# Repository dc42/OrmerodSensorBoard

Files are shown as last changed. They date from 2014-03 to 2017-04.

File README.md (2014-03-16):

OrmerodSensorBoard
==================

Here are the design files for my Z-height sensor board add-on to the RepRapPro Ormerod 3D printer. This board replaces the original IR sensor board used for Z-probing. It has the following advantages over the original:

1. It uses modulated infrared light, which makes it much less sensitive to ambient infrared such as is found in sunlight and in incandescent artificial light.
2. The sensor board is mounted on the hot end so that the sensor head is in-line with the nozzle in the x-direction. This makes it much less sensitive to variations in head sag.
3. The board includes the facility to mount the hot end connectors, eliminating the need for the original 6-pin connector. The new connectors are more reliable and more easily disassembled. In particular, the crimp receptacles can more easily be removed from the connector shell.
4. The board can accommodate three Cree LEDs to direct light on the work being printed. Alternatively, it can provide 12V power to an LED strip, or a constant-current supply to external LEDs.
5. The board includes provision for thermostatic control of the hot end fan. The fan is turned on when the hot end temperature exceeds approximately 42C, or when the board detects a hot end temperature measurement fault.
6. The board can also support an experimental ultrasonic sensor. This allows z-probing to be done anywhere on the bed. Due to variation in the speed of sound with temperature, the ultrasonic sensor is a little temperature-sensitive, but this can be compensated in the firmware.

Work is in progress to adapt the board for capacitive height sensing.

For assembly and usage instructions, please visit: http://miscsolutions.wordpress.com/assembling-and-using-the-eschertech-ormerod-hot-end-board/

I supply bare boards, kits of parts with all SMD components ready-mounted, and fully assembled boards. Contact me via the RepRap Ormerod forum at http://forums.reprap.org/list.php?340 by sending a personal message to dc42.

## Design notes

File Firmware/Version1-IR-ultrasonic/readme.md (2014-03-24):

This folder contains the following files:

<ul>
<li>OrmerodSensor.cppproj - Atmel Studio 6 project file</li>
<li>OrmerodSensor.cpp - source code</li>
<li>ecv.h - macros to make the Design-by-Contract annotations (for Escher C Verifier) in the source code invisible to the compiler</li>
</ul>

The ATTINY45A fuse settings required are: low 0xFF, high 0xDF, extended 0xFF.

The source code and the above fuse settings assume that the 12MHz ceramic resonator is fitted on the board. If the ultrasonic functionality is not required then it should be possible to omit the resonator and use the internal 8MHz clock, by changing F_CPU in the source code to 8000000uL and adjusting the fuse settings appropriately.

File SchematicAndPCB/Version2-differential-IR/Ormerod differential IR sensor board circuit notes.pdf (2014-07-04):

## Ormerod differential IR sensor board circuit description

Refer to the schematic. The board provides the following functions:
1. Illumination (U2 D1 D2 D3). U2 provides constant current drive to LEDs D1 D2 D3. The current can be increased above the default 20mA by fitting a resistor at position R23. Refer to the BCR402U datasheet for details. The +12V and 0V pads allow alternative lighting to be connected.
2. Heater on indication (B1 D7 R8). Bridge rectifier B1 allows correct operation irrespective of the polarity of the heater drive voltage. R8 limits the LED current to 20mA or less for heater voltages of up to 14V.
3. Fan control (U1 Q1 D4 R6 R7). Microcontroller U1 monitors the hot end thermistor voltage via R6. It turns the fan on via R7 and Q1 if either the temperature exceeds about 40C or the thermistor appears to be not connected. If R24 is not fitted then the firmware senses a high on pin PA4 and assumes that the Duet board uses a 1K thermistor series resistor. If R24 is fitted with a low value resistor (e.g. 1K) or a wire link, then the firmware senses a low on pin PA4 and assumes that a 4.7K series resistor is used. Series resistor R6 is included so that if either the 3.3V or the ground connection provided through connector X4 is broken, the effect on the temperature read by the Duet will be less severe and unlikely to result in serious overheating. Flyback diode D4 is included in case the fan presents an inductive load. A 0 ohm resistor or wire link can be added at position R22 if continuous operation of the fan is required.
4. Differential LED height sensor (D5 D6 D8 Q2 C1 C3 R1 R2 R3 R4 R5 R9). Microcontroller U1 measures the output from phototransistor Q2 with D6 and D5 both off, with D6 (the 'far' LED) on, and with D5 (the 'near' LED) on. Resistor R3 driving the near LED has a higher value than resistor R2 driving the far LED, to compensate for the shorter path taken by light reaching the phototransistor from the near LED. The firmware subtracts the reading with both LEDs off from each of the readings with one LED on in order to compensate for ambient IR, to provide a “far reading” and a “near reading”.

Pin PA0 on U1 determines the operating mode. The internal pullup resistor on pin PA0 is enabled, so that the pin is high if the 4th sensor wire from the Duet is not connected. When PA0 is high, the firmware operates in differential mode. When the far reading is substantially lower than the near reading, or the far reading is below a threshold, pins PA2 and PA7 are both driven low, so that the output on X4 pin 1 is 0V and the Duet sees a Z-probe reading close to zero. When the near reading is slightly below the far LED reading and the far LED reading is above threshold, PA2 is drive high and PA7 is driven low. This gives a z-probe reading of about 465. When the near reading is higher than the far reading and the far reading is above threshold, PA2 is driven low and PA7 high, resulting in a Z-probe reading of about 535. If either the near reading or the far reading is high enough to indicate that the phototransistor is saturated or approaching saturation, then both PA2 and PA7 are driven high, giving a Z probe reading close to 1023.

C3 serves not only to smooth out the supply voltage fluctuations due to the LEDs being turned on and off, but also to physically block the direct light path between the phototransistor and the photodiodes.

Resistor R9 and LED D8 provide an indication when the Z probe threshold has been reached.

If the control signal from the Duet on X4 pin 1 is driven low, then the sensor operates in simple modulated IR mode. In this mode, U1 pin PA7 is driven high if the near reading exceeds a fixed threshold. Pin PA2 remains low unless the phototransistor is saturated or approaching saturation, in which case both PA2 and PA7 are driven high to provide a Z probe reading of about 1023.
5. L1, C2 and C3 provide decoupling for U1. The ICSP pads allow U1 to be programmed.
6. Pads PAD1 through PAD7 and the pads for resistors R20 R21 are provided to facilitate modification and experimentation.

Version 1 by D Crocker, 2014-07-04.

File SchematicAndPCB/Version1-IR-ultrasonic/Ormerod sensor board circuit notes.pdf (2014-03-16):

## Ormerod sensor board circuit description

[Version 1, 2014-03-16]

Refer to the schematic. The board is designed to be populated in several different ways:
1. Modulated IR sensor, with modulation controlled by the Duet. The components fitted are:
U1 Q1 C1 C5 R2 R3 R4 R5 R13 L1 X5
The modulation signal from the Duet arrives via X5-1 and switches transistor Q2 via resistor R13. Q2 controls current flow through the IR emitter inside U1 via R5 to give a current of about 40mA when the modulation signal is high. R4 provides a base level of IR illumination even when the modulation signal is off, in order to bias the phototransistor in U1 into its linear region and reduce the effect of ambient IR. The phototransistor current causes a voltage drop across R2. C1 reduces capacitive pickup of noise from other wires in the loom. L1 and C5 decouple the incoming 3.3V supply. L1 is probably not needed n this configuration, so it could be replaced by a 0 ohm resistor. 1a. Modulated IR sensor + lighting. This is as option 1 plus the following components:
U3 D1 D2 D3 R14 X1 X2 X3 X6
In this configuration, all the hot end connectors are brought on to the board, replacing the function of the original 6-way connector. R14 completes the fan circuit. U3 provides a 20mA constant current source for LEDs D1 D2 D3. Optional resistor R1 can be added to increase the LED current, subject to keeping the current and power dissipation in U3 within its ratings.
2. Modulated IR sensor + fan control. The components populated are:
U1 U2 Q1 D4 C1 C2 C3 R2 R4 R5 R7 R10 R11 R12 L1 X1 X2 X3 X5 X6
In this mode, the modulation is controlled by the microcontroller U2, so the modulation control wire from the Duet is not needed. The microcontroller modulates the IR via R12 and Q2 (note that R13 is not fitted in this configuration). The signal appearing across R2 is fed to U2 pin 12 (ADC1) for synchronous detection. The mcu generates PWM signals at pins 6 and 8, which are combined by R7 and R10 and smoothed by C3 to provide an analog output. The mcu also controls the fan via R11 and Q1. D4 is a flyback diode for the fan, in case the fan presents an inductive load. The hot end thermistor is monitored via pin 10 of U2.
2a. Modulated IR sensor + fan + lighting. As option 2 plus U3 D1 D2 D3 and optionally R1.
3. Ultrasonic option. This is option 2 or 2a with the following additional components populated: XT1 L2 C4 R6 R8 R9
The microcontroller U2 produces a square wave at the appropriate frequency (41.67kHz) on pin 7. This is fed to the transducer connected at X4 via R6 and L2, with C4 completing the circuit while avoiding a DC bias across the transducer. R8 and R9 reduce the peak signal to remain in the range 0 to +3.3V and feed this signal to pin 11 (ADC2) of U2. U2 performs synchronous detection of the signal on this pin.
The mcu operates in IR mode when the signal at X5-1 is high or not connected, and in ultrasonic mode when the signal at X5-1 is low. A ceramic resonator is used instead of the built-in RC oscillator, in order to maintain an accurate frequency for the transducer.

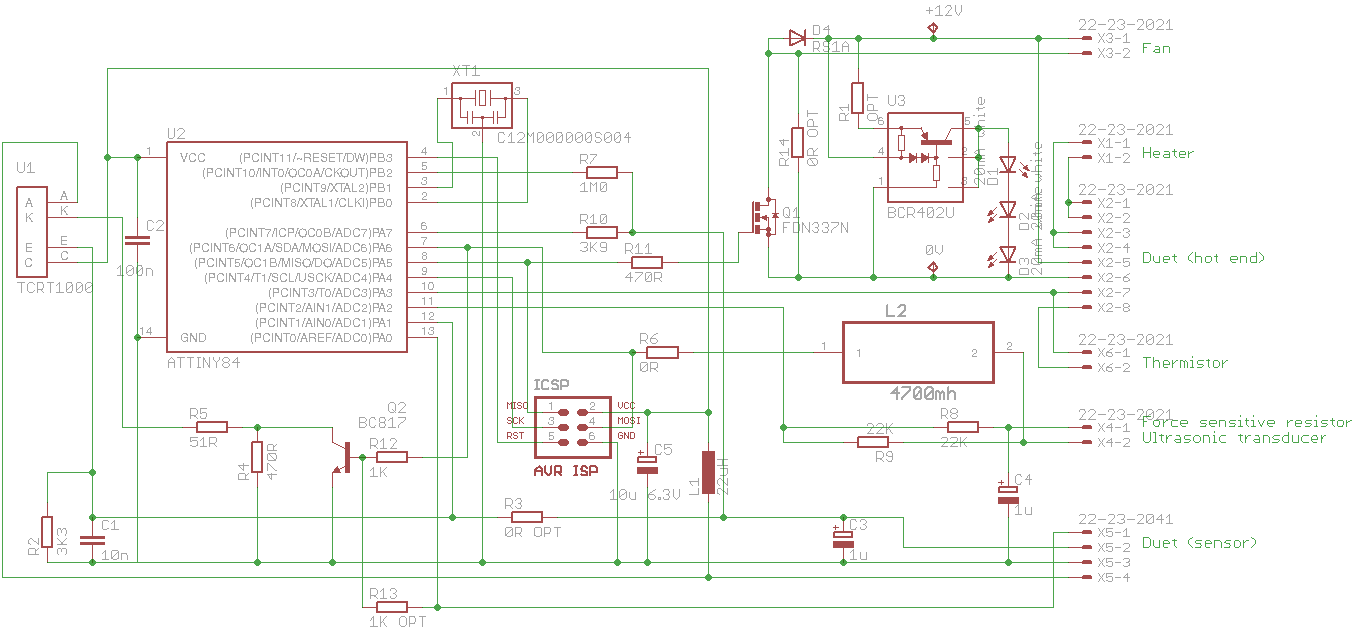
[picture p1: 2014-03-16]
SchematicAndPCB/Version1-IR-ultrasonic/schematic.png

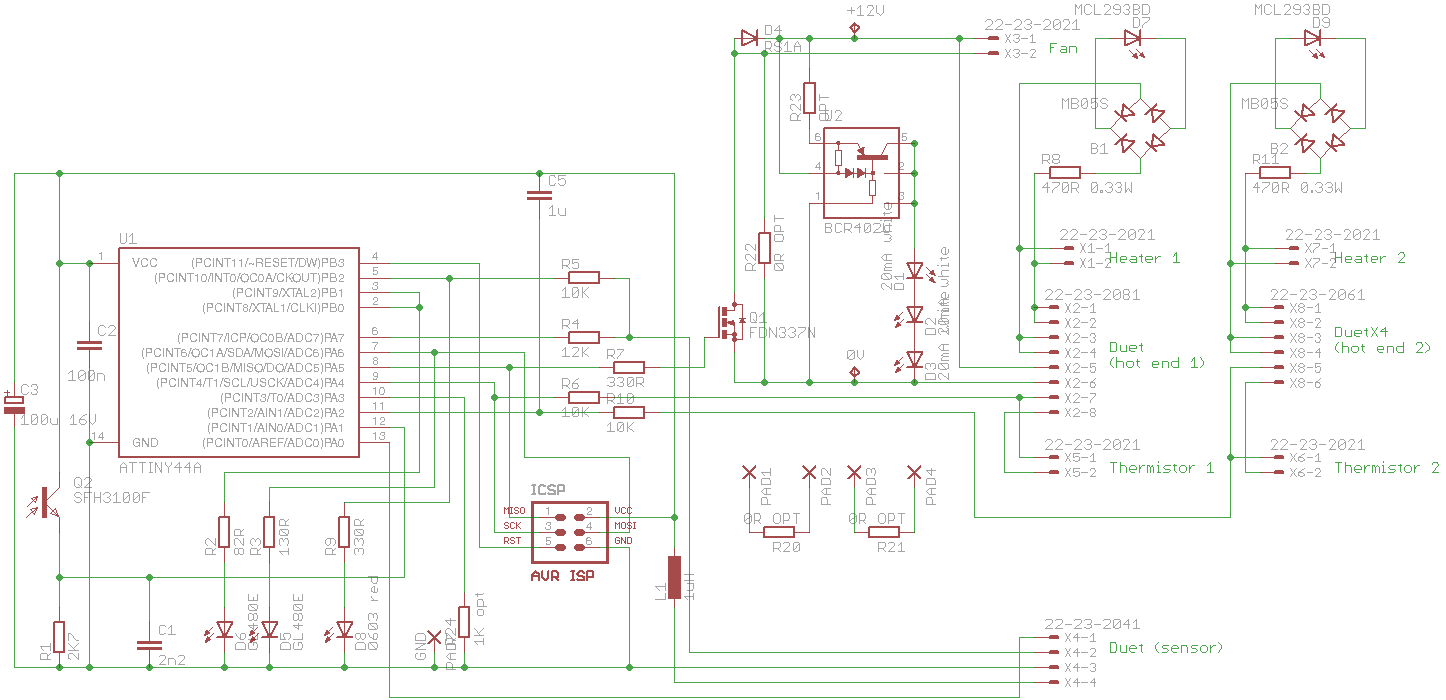
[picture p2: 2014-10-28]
SchematicAndPCB/Version2-differential-IR/schematic-dual-nozzle.png

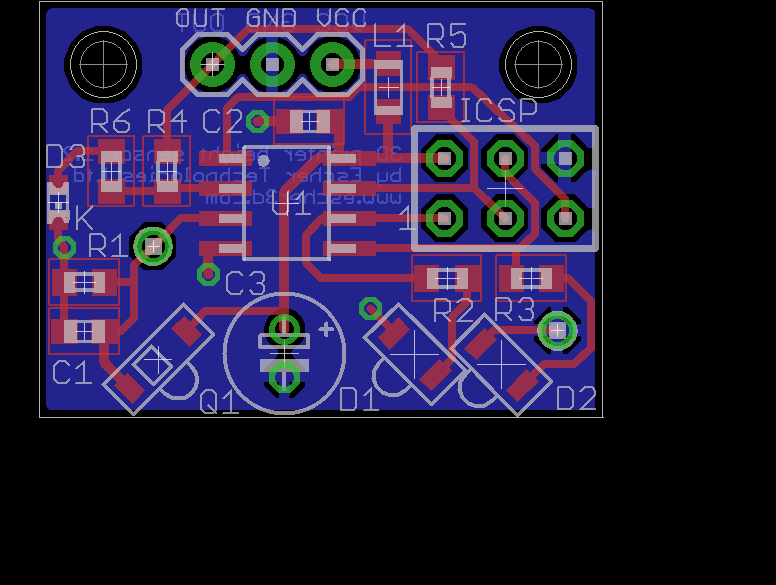
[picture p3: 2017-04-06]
SchematicAndPCB/Mini-differential-IR/V1.2/board.png

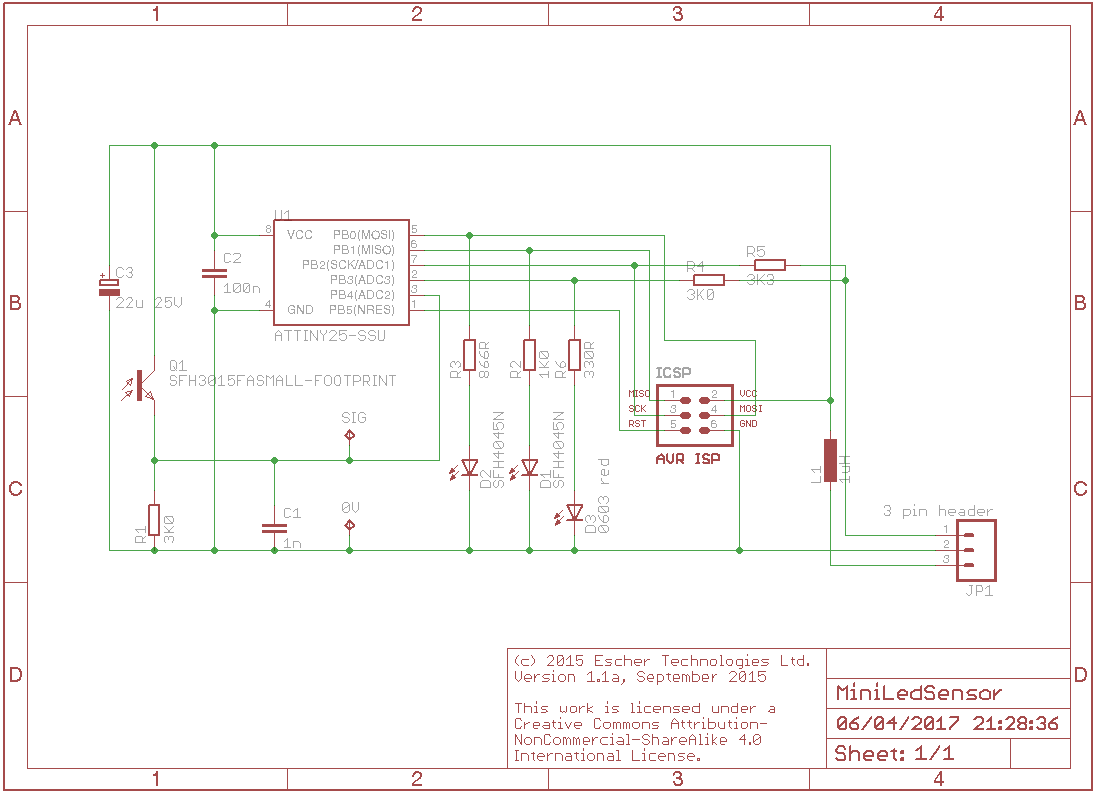
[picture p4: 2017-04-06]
SchematicAndPCB/Mini-differential-IR/V1.2/schematic.png

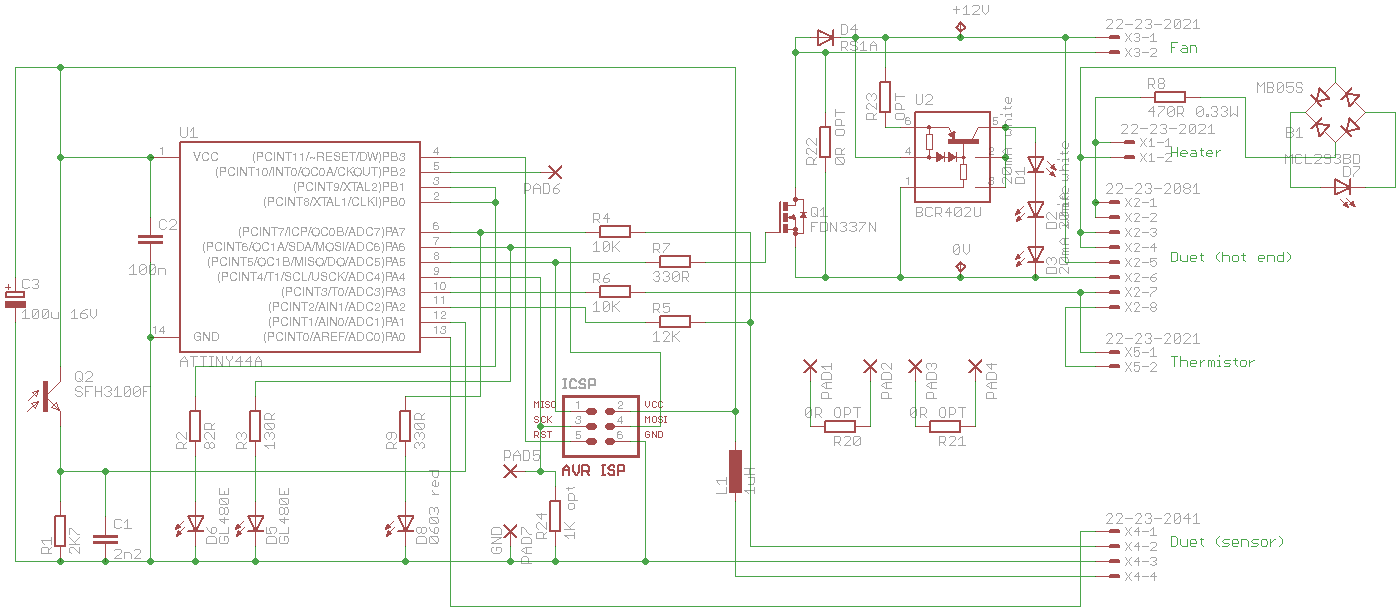
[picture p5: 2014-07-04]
SchematicAndPCB/Version2-differential-IR/schematic-single-nozzle.png

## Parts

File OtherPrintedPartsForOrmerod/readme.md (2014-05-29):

Other printed parts for Ormerod
===============================

This folder contains designs for the following printed parts, that are for the Ormerod but not for the sensor board:

1. PSU enclosure: this is an enclosure to cover the mains wiring and output wiring of a 12V 300W power supply sourced from eBay UK (http://www.ebay.co.uk/itm/UK-Stock-DC-12V-Universal-Regulated-Switching-Power-Supply-for-LED-Strip-CCTV-/161081134308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). This replaces the ATX PSU supplied with the kit and supplies a more stable and adjustable 12V supply, which is useful when printing ABS. It accommodates a snap-in IEC mains inlet with switch and fuse, a neon indicator, and a 20A locking connector for the 12V output. All of these can be sourced from Maplin Electronics or from the usual component distributors.

2. Spacers for Matt's y-belt fastening posts. Y-belt slippage is a common problem with Ormerods, and Matt's y-belt mounts at https://github.com/iamburny/OrmerodUpgrades/blob/master/y-belt-clamp-v7.stl solve the problem. However, getting the y-belt tension right can be tricky because the y-belt length can only be adjusted in multiples of a whole tooth. One solution is to print Matt's y-belt tensioning device too. A simpler solution is to print these spacers to slip under the y-belt posts before tightening the mounting screws. There are 3 different thicknesses of spacer in this print, which can be used individually or in combination to get the right y-belt tension.

3. Fan inlet duct and finger guard. This is a variation on the fan inlet duct by Andy (kwikius), designed for the 7-bladed fan shipped with some Ormerod kits, and thin enough to allow the print head to slide past the Duet electronics enclosure in its normal position. His original design is here http://forums.reprap.org/read.php?340,287558,291659#msg-291659. Hint: when fitting the Duet enclosure, push the three T-nuts into the extrusion, then rotate the one nearest the y-motor into position, then push the Duet enclosure as far towards the y-motor as it will go. By rotating the nut first, you gain a few extra mm clearance between the enclosure and the hot end fan.

4. Ormerod button push: a pair of button pushers to allow the Erase and Reset buttons to be activated through the holes in the Duet enclosure back cover.

5. X-carriage: a re-working of the X-carriage in OpenScad. This version does not have the mounting points for the IR sensor, because my own IR sensor board is mounted on the hot end instead. It has an optional slot for a force-sensitive resistor, however the area around the slot needs reinforcing if you enable this option.

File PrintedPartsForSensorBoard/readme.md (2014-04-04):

Printed parts to go with Ormerod sensor board
=============================================

To use the Ormerod sensor board you will need to print three parts:

1(a) Modified x-motor-bracket3.stl: Modified x-motor bracket. This includes an extended x-homing tab to suit the new position of the IR sensor head. Not needed if you use a microswitch for x-homing instead. Thanks to johneato for providing this.

1(b) sensorpad.stl: As an alternative to printing the modified x-motor bracket, you can print this add-on sensor pad and attach it to the original X motor bracket. Thanks to stevelup for providing this.

2(a) Modified heatsink-duct12.stl: Modified heatsink duct. This includes the mounting points for the sensor board.Thanks to johneato for providing this.

2(b) one-piece-hotend-airduct-with-new-irsensor-2.stl: Modified version of Matt's one-piece heatsink/fan duct. Thanks to Matt (iamburny) for modifying his design to add the supports and mounting holes for the sensor board. I have further modified his design by replacing the T-shaped cable tie point at the top centre by a cable tie loop at the top right, and making the cable management piece stronger. To use the one-piece duct you need to drill an additional hole in the heatsink so that you can rotate it 90 degrees.

3(a) Insulator.stl: This prevents the board from shorting against the z-threaded rod or other metal parts if the print head moves beyond the intended x-homing position. Alternatively, for kit 2 or 3 you can use Kim brown's safety cover, his files are at http://www.thingiverse.com/thing:272634.

3(b) Insulator-for-ultrasonic.stl: Thicker insulator which includes a holder for the ultrasonic transducer. This is thicker and longer than Insulator.stl to ensure that it touches the Z-nut trap before the ultrasonic sensor touches the threaded rod. If you use this part, you may have to extend the x-homing tab even further in the X-direction than the modified x-motor bracket already does, for example by sticking a piece of white card on top of it.

3(c) Insulator-thick.stl: Thick insulator, for use when the ultrasonic sensor is glued on the pcb behind and slightly to the left of the IR sensor.

Also in this folder:

BoardHolder.stl: This can be fixed to the back of a solder stencil, allowing boards to be accurately aligned with the stencil prior to application of solder paste.

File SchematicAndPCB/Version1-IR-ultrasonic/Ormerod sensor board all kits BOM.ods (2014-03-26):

Ormerod sensor board BOM |  | Last revision 2014-03-26
 |  |  |  | ------------- Qty required ------------
Item | Value or part # | Designators | Farnell # | Kit 2 | Kit 3 | Kit 4 | Kit 4+ | Kit 5 | Notes
Through hole parts
Connector | Molex 22-23-2021 | X1 X3 X4 X6 | 1462926 |  | 3 | 3 | 3 | 4 | X4 fitted on kit 5 only
Connector | Molex 22-23-2041 | X5 | 1462920 | 1 | 1 | 1 | 1 | 1
Connector | Molex 22-23-2081 | X2 | 1756826 |  | 1 | 1 | 1 | 1
Connector | 2x3 header | ICSP |  |  |  |  |  |  | Not fitted - only needed for programming
Sensor | TCRT1000 | U1 | 1470064 | 1 | 1 | 1 | 1 | 1
LED | Cree C535A-WJN-CU0V0231 | D1 D2 D3 | 1855547 |  | 3 | 3 | 3 | 3
Capacitor | 3.3nF 10% ceramic X7R | - | 1216424 |  |  |  |  | 0 or 1 | See note 1
Non-mounted parts
10mm 40kHz xmtr | Multicomp MCUST10P40B07RO |  | 2362667 |  |  |  |  | 1 | See note 1
Shell | Molex 22-01-2025 |  | 143126 |  | 3 | 3 | 3 | 4
Shell | Molex 22-01-2045 |  | 143128 | 1 | 1 | 1 | 1 | 1
Shell | Molex 22-01-2085 |  | 143130 |  | 1 | 1 | 1 | 1
Crimp pins | Molex 08-50-0032 |  | 9731474 | 4 | 18 | 18 | 18 | 20 | Plus a few spares
2way shell | Multicomp 2226A-02 |  | 1593506 | 1 | 1 |  |  | 1
Crimp pins | Multicomp 2226TG |  | 1593529 | 1 | 1 |  |  | 1
1m white wire 10/0.1 |  |  |  | 1 | 1 |  |  | 1
Screw | M2.5x10mm countersunk |  |  | 2 | 2 | 2 | 2 | 2
SMD parts
IC | ATTINY44A-SSU | U2 | 1699395 |  |  | 1 | 1 | 1
IC | BCR402U | U3 | 1791063 |  | 1 | 1 | 1 | 1
Transistor | BC817-40 | Q2 | 1798081 | 1 | 1 | 1 | 1 | 1
Mosfet | FDN337N | Q1 | 9845356 |  |  | 1 | 1 | 1
Diode | RS1A | D4 | 4085000 |  |  | 1 | 1 | 1 | Flyback diode for fan
12MHz resonator | AEL C12M000000S004 | XT1 | 1448144 |  |  |  | 1 | 1 | Alternative part AWSCR-12.00CV-T
Inductor | 1uH TDK MLZ2012A1R0WT | L1 | 2215638 | 1 | 1 | 1 | 1 | 1 | Must have low enough resistance
Inductor | 4.7mH EPCOS B82442H1475K | L2 | 3877474 |  |  |  | 1 | 1 | For driving ultrasonic transducer
Capacitor | 10u 6.3V tantalum case A | C5 | 1754143 | 1 | 1 | 1 | 1 | 1
Capacitor | 1u 1206 tantalum 10V+ 10% | C3 C4 | 1457411 |  |  | 1 | 2 | 2
Capacitor | 10n 0603 X7R | C1 | 1759022 | 1 | 1 | 1 | 1 | 1
Capacitor | 100n 0603 X7R | C2 | 1759016 |  |  | 1 | 1 | 1
Resistor | 0R 0603 | R3 |  | 1 | 1 |  |  |  | For direct sensor connection when U2 not fitted
Resistor | 0R 0603 | R6 |  |  |  |  | 1 | 1 | To reduce ultrasonic transducer drive if needed
Resistor | 0R 0603 | R14 |  |  | 1 |  |  |  | Bypasses fan control when Q1 not fitted
Resistor | 51R 0603 | R5 |  | 1 | 1 | 1 | 1 | 1
Resistor | 470R 0603 | R4 |  | 1 | 1 | 1 | 1 | 1
Resistor | 470R 0603 | R11 |  |  |  | 1 | 1 | 1
Resistor | 1K 0603 | R12 |  |  |  | 1 | 1 | 1
Resistor | 1K 0603 | R13 |  | 1 | 1
Resistor | 3K3 0603 | R2 |  | 1 | 1 | 1 | 1 | 1
Resistor | 3K9 0603 | R10 |  |  |  | 1 | 1 | 1
Resistor | 22K 0603 | R8 R9 |  |  |  |  | 2 | 2 | See note 1
Resistor | 1M0 0603 | R7 |  |  |  | 1 | 1 | 1
Resistor | As required 0603 | R1 |  |  |  |  |  |  | For increasing LED current
Notes
1 | Kit 5 early uses alternative ultrasonic transducer Murata MA40S4S (Farnell part number 1777667, also available from RS and from Conrad Electronics). This transducer produces less output, so the value of R8 is changed to 1M. A capacitor of about 3.3nF needs to be connected in parallel with this transducer to tune it. The Multicomp transducer does not require a tuning capacitor.

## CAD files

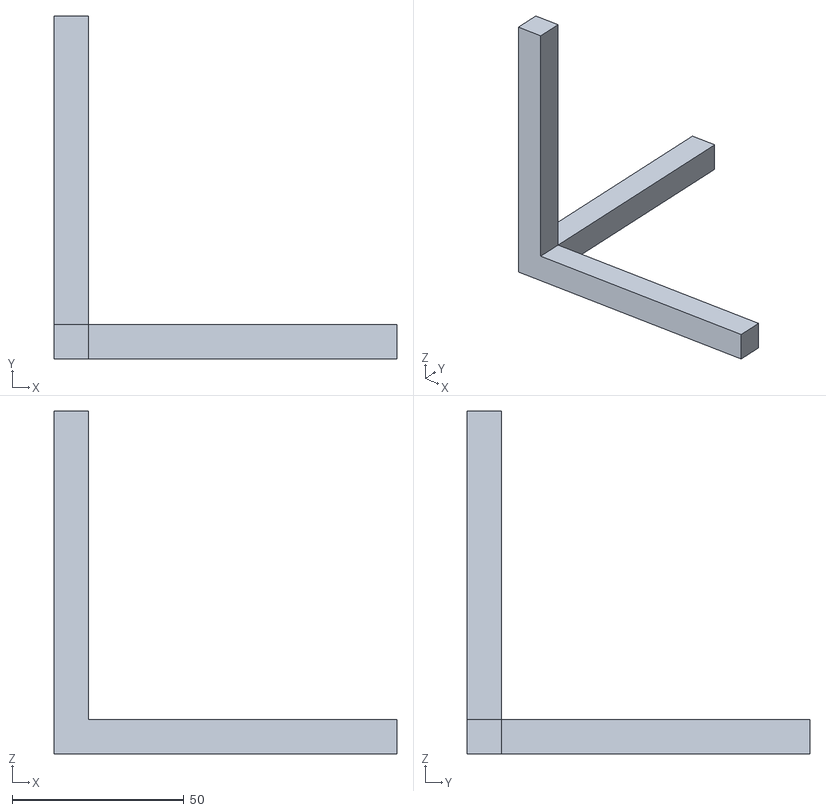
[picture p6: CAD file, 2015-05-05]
OtherPrintedPartsForOrmerod/OrthogonalCalibrationPiece.stl
100.0 x 100.0 x 100.0

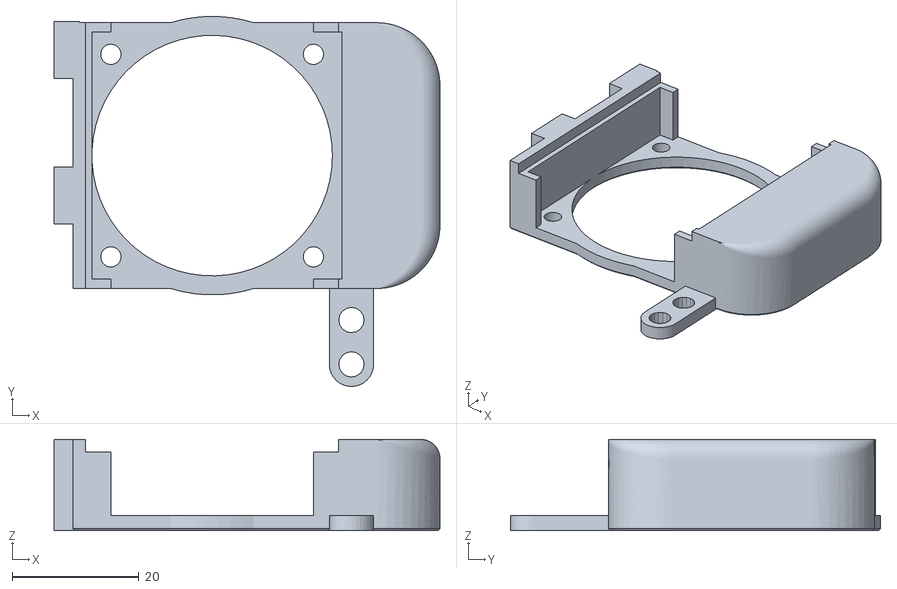
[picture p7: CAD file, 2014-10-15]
PrintedPartsForSensorBoard/modified-heatsink-duct-0.5mm-lower.stl
61.0 x 58.5 x 14.4

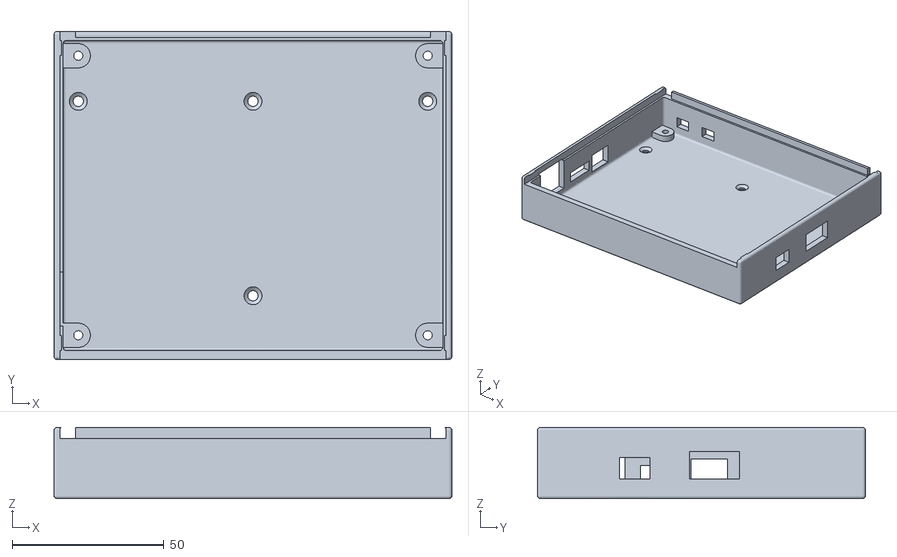
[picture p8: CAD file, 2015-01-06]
OtherPrintedPartsForOrmerod/DuetEnc-MiniKossel.stl
131.0 x 108.0 x 23.5

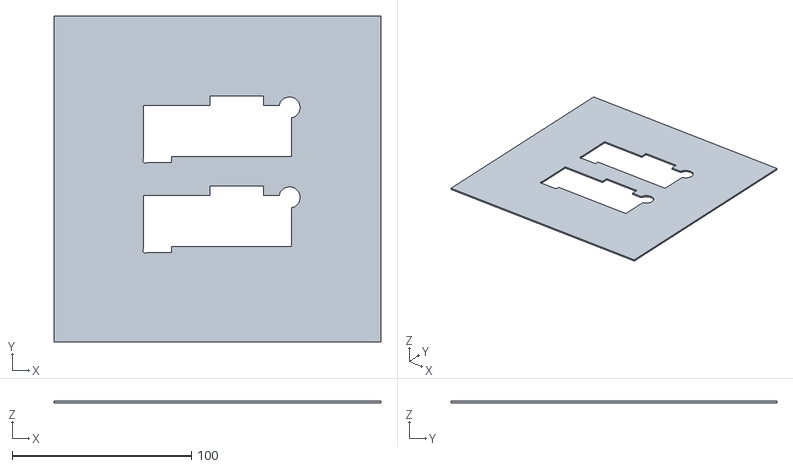
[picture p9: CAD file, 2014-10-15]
PrintedPartsForSensorBoard/BoardHolder-diff-led.stl
182.4 x 181.8 x 1.10

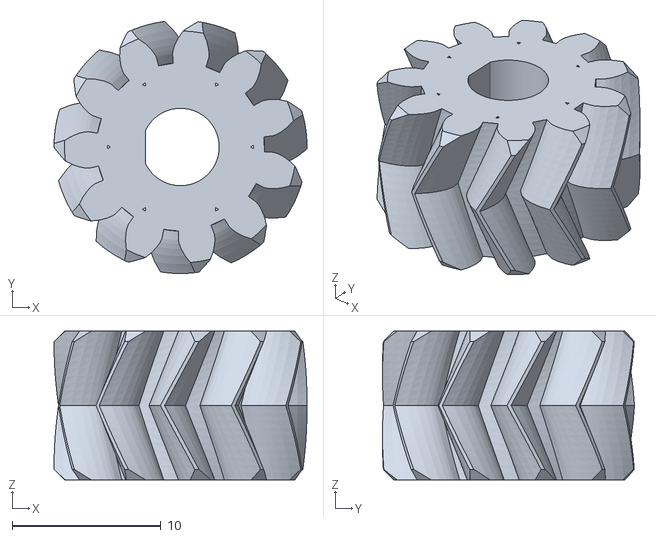
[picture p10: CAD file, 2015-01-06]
OtherPrintedPartsForOrmerod/iamburnyExtruderSmallGearModified.stl
17.0 x 17.0 x 10.0

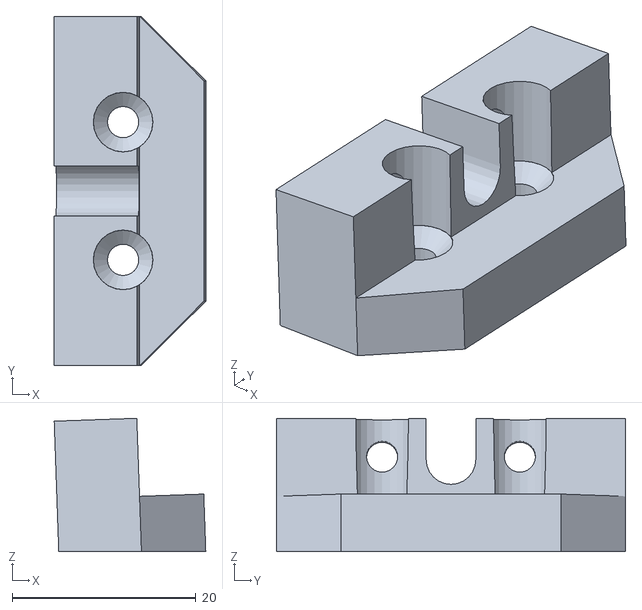
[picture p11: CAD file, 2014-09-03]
OtherPrintedPartsForOrmerod/NozzleMountStandard-2deg.stl
16.5 x 38.0 x 14.5

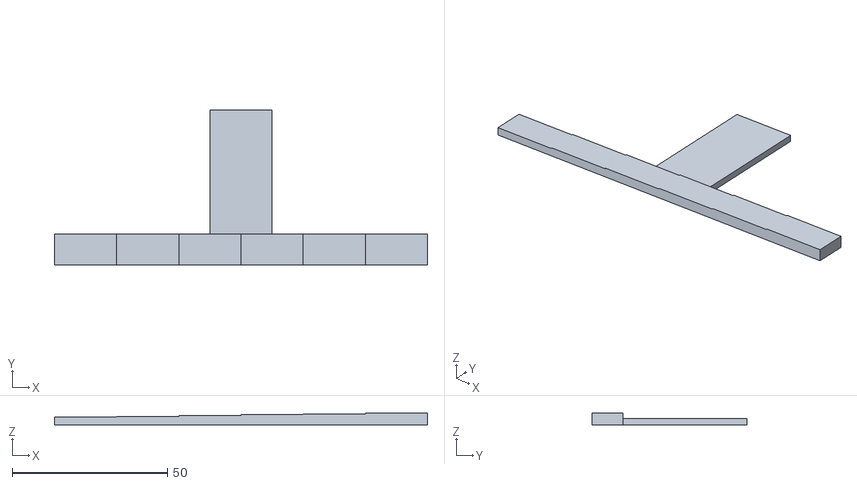
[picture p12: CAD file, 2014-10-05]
PrintedPartsForSensorBoard/LedBoardTestJig.stl
120.0 x 50.0 x 3.75

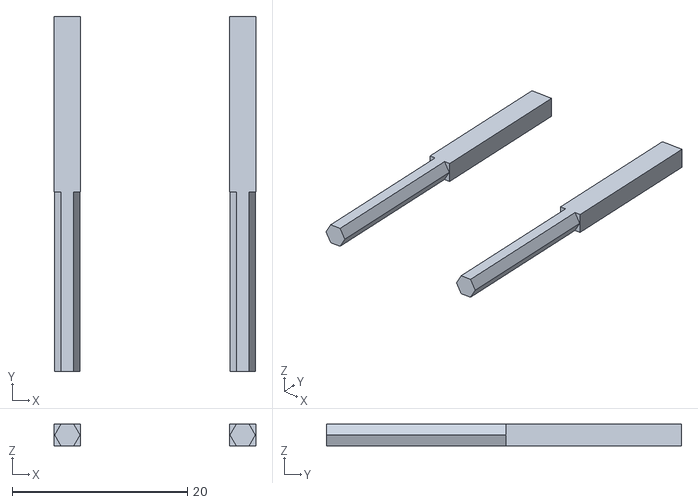
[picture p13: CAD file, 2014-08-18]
OtherPrintedPartsForOrmerod/OrmerodButtonPush.stl
23.0 x 40.5 x 2.50

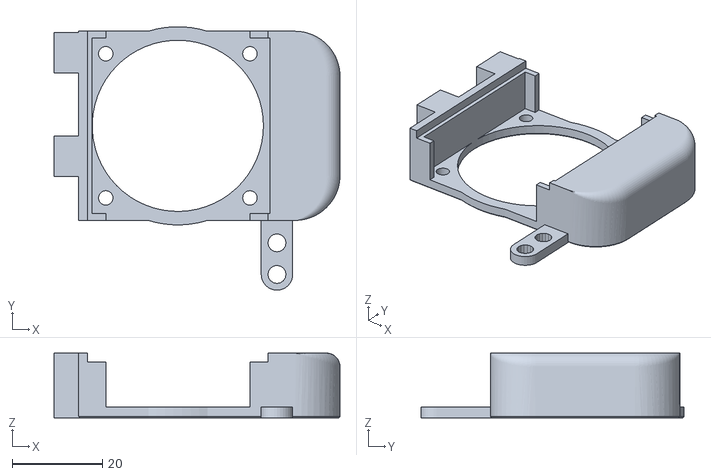
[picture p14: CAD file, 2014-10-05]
PrintedPartsForSensorBoard/modified-heatsink-duct-dual-nozzle.stl
63.5 x 58.5 x 14.4

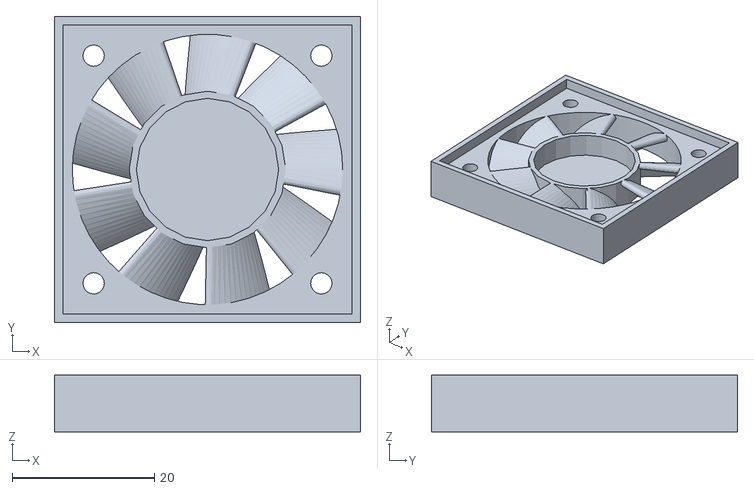
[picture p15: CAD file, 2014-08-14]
OtherPrintedPartsForOrmerod/FanDeflector.stl
43.0 x 43.0 x 8.00

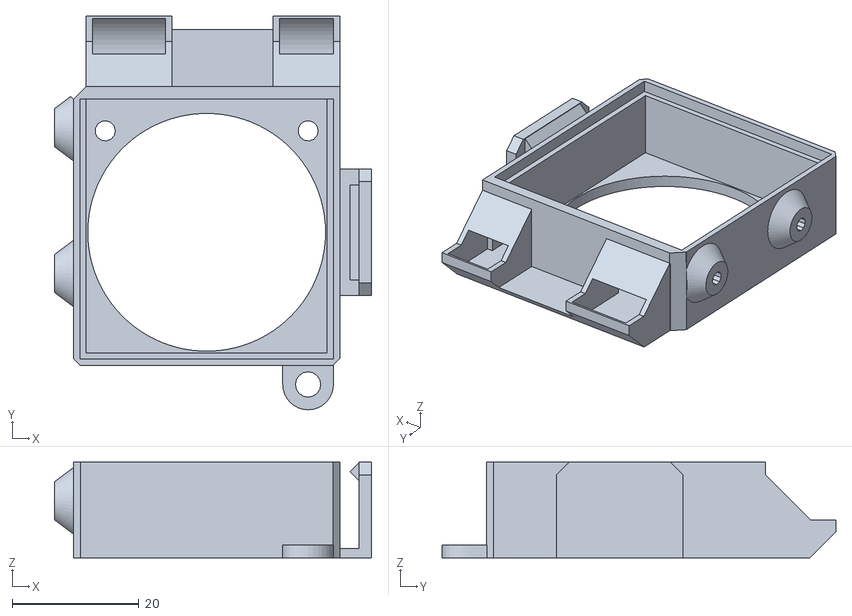
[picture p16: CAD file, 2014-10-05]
PrintedPartsForSensorBoard/one-piece-hotend-airduct-with-new-irsensor-1mm-lower.stl
50.0 x 62.1 x 15.1

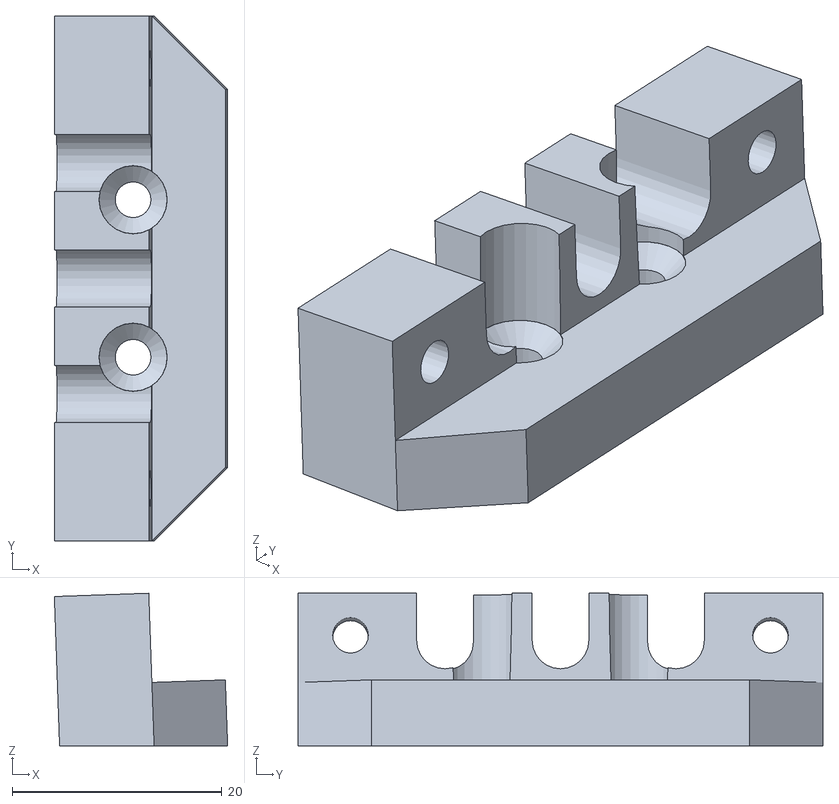
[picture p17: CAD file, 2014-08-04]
OtherPrintedPartsForOrmerod/NozzleMount-1or2-2deg.stl
16.5 x 50.0 x 14.5

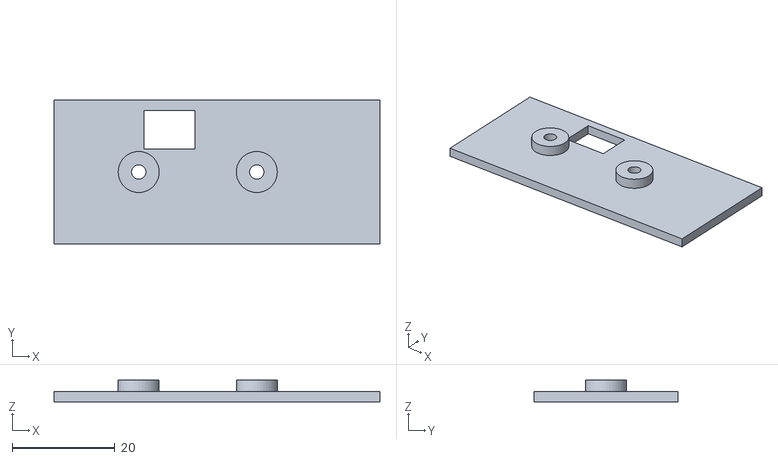
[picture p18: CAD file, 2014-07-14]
PrintedPartsForSensorBoard/Insulator-diff-led-dual-nozzle.stl
63.5 x 28.0 x 4.25

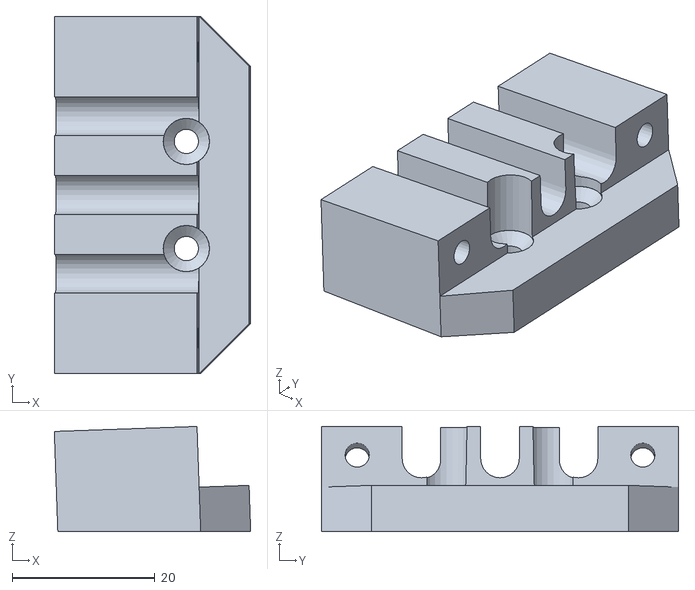
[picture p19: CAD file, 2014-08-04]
OtherPrintedPartsForOrmerod/NozzleMount-1or2-2deg-long.stl
27.5 x 50.0 x 14.7

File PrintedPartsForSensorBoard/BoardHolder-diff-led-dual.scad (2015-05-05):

// Holder for Ormerod prototype differential IR sensor board
// Choose layer height to be a submultiple of the thickness

thickness=1.1;	// board is 1.2mm but this part comes out slightly too thick
xborder=30;
yborder=30;
yrepeat=70;
height=82.07375;
width=29.00;
nibWidth=3.0;
nibHeight=15.5;	//actually 14.605
upperWidth=43.35;
upperHeight=38;
clearance=0.35;
cornerRadius=1.5;
cornerOffset=1;
overlap=1;

module wedge(x,y,z)
{
	polyhedron(
		points=[[0,0,0],[x,0,0],[0,y,0],[0,0,z],[x,0,z],[0,y,z]],
		faces=[[0,2,1],[3,4,5],[0,1,3],[1,4,3],[1,2,4],[2,5,4],[0,3,2],[5,2,3]]
	);
}

module boardCutout()
{
	translate([0,nibWidth,-overlap])
		cube([height+clearance,width+clearance,thickness+2*overlap]);
	translate([height-upperHeight,nibWidth,-overlap])
		cube([upperHeight+clearance,upperWidth+clearance,thickness+2*overlap]);
	translate([0,0,-overlap])
		cube([nibHeight,nibWidth+overlap,thickness+2*overlap]);
	translate([height+clearance-cornerOffset,upperWidth+nibWidth+clearance-cornerOffset,-overlap])
		cylinder(r=6,h=thickness+2*overlap,$fn=12);
}


difference()
{
	cube([height+2*xborder+clearance,upperWidth+nibWidth+2*yborder+clearance+yrepeat,thickness]);
	translate([xborder,yborder,0]) boardCutout();
	translate([xborder,yborder+yrepeat,0]) boardCutout();
}

translate([12-overlap,16-overlap,0]) wedge(10+2*overlap,10+2*overlap,thickness);

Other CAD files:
PrintedPartsForSensorBoard/modified-heatsink-duct-single-nozzle.stl
PrintedPartsForSensorBoard/original-rrp-fan-duct.stl
OtherPrintedPartsForOrmerod/DuetEncX4.stl
PrintedPartsForSensorBoard/modified-fan-duct.stl
PrintedPartsForSensorBoard/BoardHolder-diff-led-mini.scad
PrintedPartsForSensorBoard/BoardHolder-diff-led.scad
PrintedPartsForSensorBoard/BoardHolder.scad
OtherPrintedPartsForOrmerod/DuetEnc-MiniKossel.scad
OtherPrintedPartsForOrmerod/DuetEnc.scad
OtherPrintedPartsForOrmerod/DuetEnc.stl
OtherPrintedPartsForOrmerod/DuetEncMeasure.scad
OtherPrintedPartsForOrmerod/FanDeflector.scad
OtherPrintedPartsForOrmerod/NozzleMount.scad
OtherPrintedPartsForOrmerod/NozzleMount.stl
OtherPrintedPartsForOrmerod/OrmerodButtonPush.scad
OtherPrintedPartsForOrmerod/OrthogonalCalibrationPiece.scad
OtherPrintedPartsForOrmerod/PSU.scad
OtherPrintedPartsForOrmerod/PSU.stl
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

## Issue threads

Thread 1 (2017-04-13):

Schematic note

timmit99, 2017-04-13:
Just looking through for replacement part numbers and it seems that on the V1.2 differential sensor board schematic you did not change the Version number in the  V1.2 schematic. It still says V1.1a, September 2015.

There is no indication other than the file's path that it is ACTUALLY the V1.2 schematic.

timmit99, 2017-04-13:
https://raw.githubusercontent.com/dc42/OrmerodSensorBoard/master/SchematicAndPCB/Mini-differential-IR/V1.0_1.1/schematic.png

https://raw.githubusercontent.com/dc42/OrmerodSensorBoard/master/SchematicAndPCB/Mini-differential-IR/V1.2/schematic.png

dc42, 2017-04-13:
You are right, I forgot to update the version number in the text on the schematic. But it's definitely the version 1.2 schematic, it has the right part numbers for the phototransistor and IR LEDs.

timmit99, 2017-04-13:
thanks, Just bashed into the sensor and bent one of the IR LED's back and when i tried to reorient it the legs snapped. I got 2 of them on the way from Mouser.

dc42, 2017-04-13:
If the IR LEDs have legs then you have the version 1.0 or 1.1 board. The part numbers on the 1.2 schematic are SMD parts that won't fit your board.

timmit99, 2017-04-13:
Yep, that's why i was checking the two versions because we have one V1.1 and one V1.2 board. That's when i noticed that the version numbering was off and just wanted to post here to avoid any further confusion. The broken board is a V1.1 so i have the sfh4141 coming. Thanks for the awesome board!

Closed 2017-04-13.

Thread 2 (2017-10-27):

v1.3 hardware is out but schematics are missing here.

lf-, 2017-10-27:
[Spool3D](https://spool3d.ca/mini-differential-ir-height-sensing-board/) says that they have "v1.3" boards, but I only see v1.2 here if the commit history is to be believed.

Also, the link to the schematic PNG in [this blog post](https://miscsolutions.wordpress.com/mini-height-sensor-board/) is broken.

dc42, 2017-10-28:
The schematic for version 1.3 is the same as for version 1.2. Only the PCB layout is different.

amrithmmh, 2018-04-24:
can you share the schematics? the link seems broken

amrithmmh, 2018-04-24:
thanks for making the circuit
Is this possible to use it with glass (stuck with 3M blue tape on top) ?

lf-, 2018-04-24:
Consider reading the blog post detailing the project [here](
https://miscsolutions.wordpress.com/mini-height-sensor-board/) which states
supported surface types.

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

Deneteus, 2019-01-27:
Why were changes needed for the PCB layout between 1.2 and 1.3 if the schematic was the same?

dc42, 2019-01-28:
To make manufacturing easier.

Deneteus, 2019-01-31:
Is there any reason it cannot be made smaller? Say doing the same design but with edge mounted SMD sensors?

dc42, 2019-01-31:
The width could be slightly smaller, it is limited by the spacing needed between the phototransistor and the outer IR diode. The height could be reduced by using a attiny44a MCU in a flat pack package instead of attiny25 and smaller connectors and programming pads, or perhaps a single 6-way connector for both. We intended to switch to a JST 1.5mm connector but we had push back from one of our OEM customers.

Closed 2019-04-06.

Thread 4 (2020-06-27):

Hardcode to digital output mode

3dlpm, 2020-06-27:
Hi,

I am using the Escher 3D mini IR sensor board (V1.2) with a RUMBA board, which has a three pin Z- endstop connectors. It provides 5V on VCC, GND and has a signal input, which can be internally pulled up. Using the rumba with Marlin would easily work, but I am using the RUMBA with Klipper firmware, which runs on a separate host CPU (Raspberry Pi) and controls the RUMBA, which has a small version of firmware that executes the motion commands that the Klipper host sends it.

I am having issues with the mini sensor board starting in analog output mode (4 LED flashes) because Klipper sometimes takes a while to start (or restart, if you changed config) so the firmware in the RUMBA does not set the internal pull-ups on the Z- signal pin on time for the mini-sensor board to detect.
I basically have to cycle the power or disconnect the mini board connectors every time, sometimes repeatedly, until the internal pull-ups are set by klipper. It is very annoying and inconsistent to get the mini-sensor board started in digital output mode.

I would like to simply hard code the mini sensor board so that it always starts in digital output mode. I am not a programmer and I don't have enough knowledge to modify/verify and upload the mini sensor board's firmware. Do you have a workaround or suggestion for how to hard code the sensor board to always start in digital mode?

I think this is something that should be implemented as a jumper (solder) on the board.

Thank you

dc42, 2020-06-27:
Hi,

Why not add an external pullup resistor between OUT and VCC? That would
be easier than reprogramming it.

Regards

David Crocker, Escher Technologies Ltd.
http://www.eschertech.com
Tel. +44 (0)20 8144 3265 or +44 (0)7977 211486

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

3dlpm, 2020-06-27:
Yes, I could try that. What value do you recommend?

dc42, 2020-06-27:
I suggest between 20K and 100K.

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

--
Sent from my Android device with K-9 Mail. Please excuse my brevity.

3dlpm, 2020-06-29:
Thanks David.
It is working fine with a 39Kohm external pull-up

Closed 2020-06-29.

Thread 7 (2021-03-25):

Calibration of DIY version of your sensor

deHarro, 2021-03-25:
Hi David, @dc42

I built a clone IR-sensor from the schematics you provided.
It sort of works, but I think I have to do some calibration before I get decent results.
Is there any calibration instruction available, you can provide me with, please?

Thanks!
Harry

deHarro, 2021-04-18:
I realized that the calibration data are never read back from EEPROM, so perhaps this calibration thing is not use at all.

Harry

Closed 2021-04-18.

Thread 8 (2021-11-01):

TMC2209/UART + ir sensor has inconsistent readings.

mpalpha, 2021-11-01:
What component do I need and where do I add it? to block the interference?

mpalpha, 2021-11-02:
Trying a 25v 47uf capacitor between. Gnd/5v pins. Hope it works.

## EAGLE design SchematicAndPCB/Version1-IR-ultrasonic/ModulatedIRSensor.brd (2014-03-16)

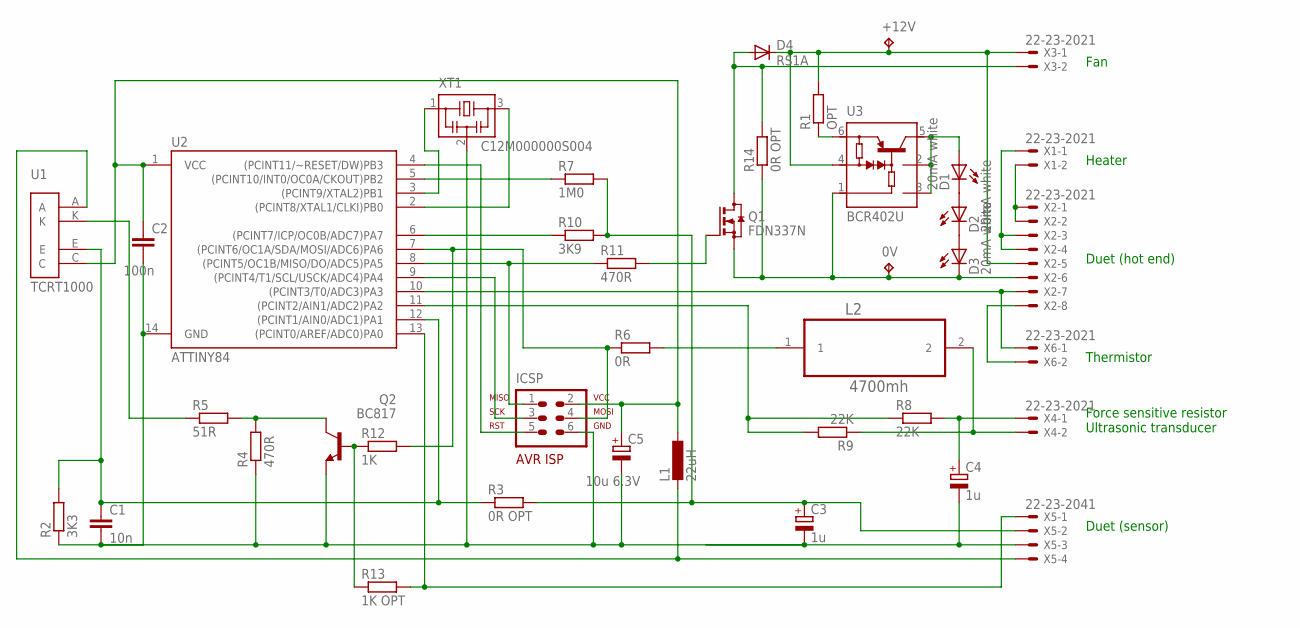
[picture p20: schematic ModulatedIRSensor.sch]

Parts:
0V: TPPAD1-13; P1-13
+12V: TPPAD1-13; P1-13
C1: 10n; C0603
C2: 100n; C0603
C3, C4: 1u; SMC_A
C5: 10u 6.3V; SMC_A
D1, D2, D3: 20mA white; LED5MM
D4: RS1A; DO214AC
ICSP: AVR-ISP-6VERT; AVR-ISP-6
L1: 22uH; L2012C
L2: 4700mh; INDC5650X530N
Q1: FDN337N; SOT23
Q2: BC817; SOT23
R1: OPT; R0603
R2: 3K3; R0603
R3, R14: 0R OPT; R0603
R4, R11: 470R; R0603
R5: 51R; R0603
R6: 0R; R0603
R7: 1M0; R0603
R8, R9: 22K; R0603
R10: 3K9; R0603
R12: 1K; R0603
R13: 1K OPT; R0603
U1: TCRT1000
U2: ATTINY84; SO14
U3: BCR402U; SC74_INFINEON
X1, X3, X4, X6: 22-23-2021
X2: 22-23-2021; 22-23-2081
X5: 22-23-2041
XT1: C12M000000S004; CSTCR6M

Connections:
GND: C1.2, C2.2, C3.-, C4.-, C5.-, ICSP.6, Q2.2 (E), R2.1, R4.1, U2.14 (GND), X5.3, XT1.2
GND2: 0V.TP, D3.K (C), Q1.2 (S), R14.1, U3.1 (GND), X2.6
LED: D1.A, U3.2 (IOUT2), U3.3 (IOUT3), U3.5 (IOUT1)
unnamed: L1.2, U1.A, X5.4
unnamed: L2.2, R9.1, X4.2
unnamed: ICSP.5, U2.4 ((PCINT11/~RESET/DW)PB3)
unnamed: ICSP.1, R11.1, U2.8 ((PCINT5/OC1B/MISO/DO/ADC5)PA5)
unnamed: ICSP.3, U2.9 ((PCINT4/T1/SCL/USCK/ADC4)PA4)
unnamed: ICSP.4, R6.1, R12.2, U2.7 ((PCINT6/OC1A/SDA/MOSI/ADC6)PA6)
unnamed: R1.1, U3.6 (REXT)
unnamed: D1.K (C), D2.A
unnamed: U2.10 ((PCINT3/T0/ADC3)PA3), X2.7, X6.1
unnamed: X1.2, X2.1, X2.2
unnamed: D2.K (C), D3.A
unnamed: C3.+, R3.2, R7.2, R10.2, X5.2
unnamed: D4.A, Q1.3 (D), R14.2, X3.2
unnamed: X1.1, X2.3, X2.4
unnamed: X2.8, X6.2
unnamed: R5.1, U1.K
unnamed: L2.1, R6.2
unnamed: Q2.3 (C), R4.2, R5.2
unnamed: R7.1, U2.5 ((PCINT10/INT0/OC0A/CKOUT)PB2)
unnamed: C4.+, R8.2, X4.1
unnamed: R10.1, U2.6 ((PCINT7/ICP/OC0B/ADC7)PA7)
unnamed: R8.1, R9.2, U2.11 ((PCINT2/AIN1/ADC2)PA2)
unnamed: Q1.1 (G), R11.2
unnamed: Q2.1 (B), R12.1, R13.1
unnamed: C1.1, R2.2, R3.1, U1.E, U2.12 ((PCINT1/AIN0/ADC1)PA1)
unnamed: R13.2, U2.13 ((PCINT0/AREF/ADC0)PA0), X5.1
unnamed: U2.2 ((PCINT8/XTAL1/CLKI)PB0), XT1.3
unnamed: U2.3 ((PCINT9/XTAL2)PB1), XT1.1
VCC: C2.1, C5.+, ICSP.2, L1.1, U1.C, U2.1 (VCC)
VS+12V: +12V.TP, D4.C, R1.2, U3.4 (VIN), X2.5, X3.1

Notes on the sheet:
Heater
Duet (hot end)
Thermistor
Duet (sensor)
Force sensitive resistor Ultrasonic transducer
Fan
TCRT1000

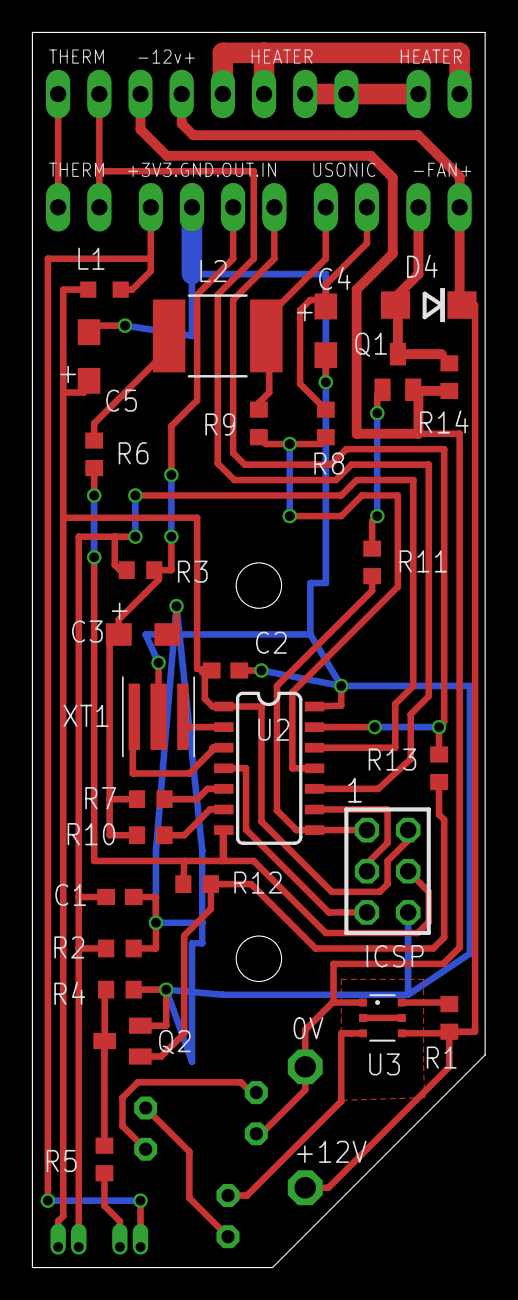
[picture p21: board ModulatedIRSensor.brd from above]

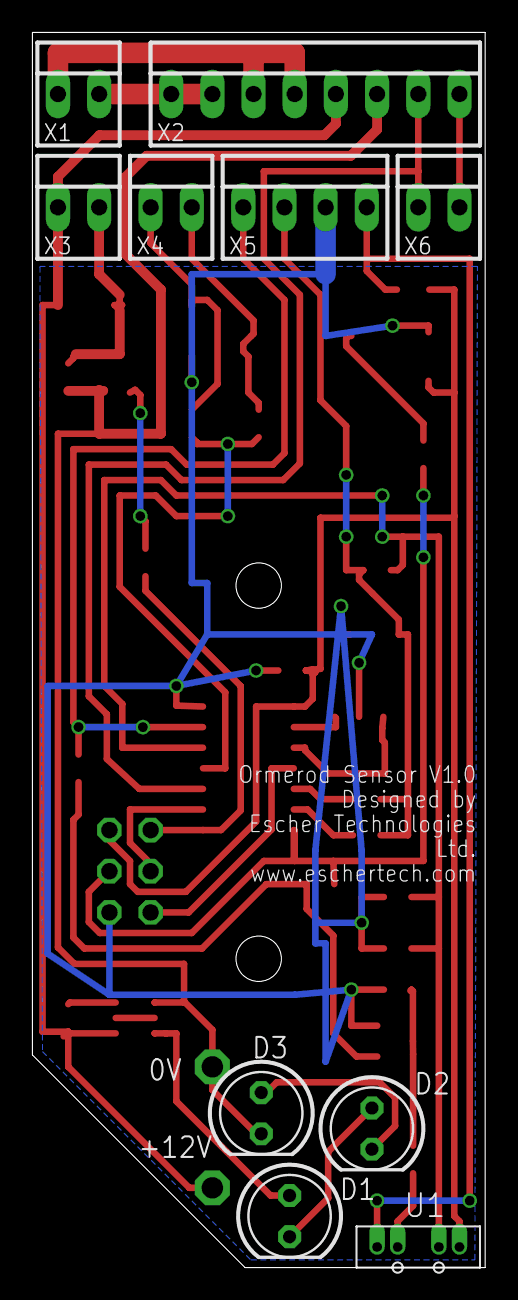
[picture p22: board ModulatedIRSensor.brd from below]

Board: 2 copper layers, 27.9 x 76.2 mm, 40 parts (12 on the bottom side), 33 nets.

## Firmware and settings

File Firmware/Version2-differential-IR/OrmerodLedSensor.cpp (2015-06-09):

/*
 * OrmerodLedSensor.cpp
 *
 * Created: 16/02/2014 21:15:50
 *  Author: David
 */ 

#include <ecv.h>

#ifdef __ECV__
#define __attribute__(_x)
#define __volatile__
#define __DOXYGEN__				// this avoids getting the wrong definitions for uint32_t etc.
#endif

#ifdef __ECV__
#pragma ECV noverifyincludefiles
#endif

#include <avr/io.h>
#include <avr/interrupt.h>
#include <avr/eeprom.h>
#include <avr/wdt.h>

#ifdef __ECV__
#pragma ECV verifyincludefiles
#endif

#define DUAL_NOZZLE (1)		// set nonzero for dual nozzle support
#define ISR_DEBUG	(0)		// set nonzero to use PB2 as debug output pin

#if DUAL_NOZZLE && ISR_DEBUG
#error "DUAL_NOZZLE and ISR_DEBUG may not both be set"
#endif

#define BITVAL(_x) static_cast<uint8_t>(1u << (_x))

// Pin assignments:
// PA0/ADC0		digital input from Duet
// PA1/ADC1		analog input from phototransistor
// PA2/ADC2		output to Duet via 12K resistor (single nozzle) OR analog input from thermistor2 (dual nozzle)
// PA3/ADC3		analog input from thermistor (single nozzle) or 1K/4K7 sense pin (dual nozzle)
// PA4/SCLK		1K/4K7 sense pin (single nozzle) or analog input from thermistor 1 (dual nozzle). Also SCLK when programming.
// PA5/OC1B		digital output to control fan, active high. Also MISO when programming.
// PA6/OC1A		near LED drive, active low in prototype, will be active high in release. Also MOSI when programming.
// PA7/OC0B		output to Duet via 10K resistor

// PB0			far LED drive, active high
// PB1			far LED drive, active high (paralleled with PB0)
// PB2/OC0A		unused (single nozzle) OR ISR-DEBUG pin OR output to Duet via 12K resistor (dual nozzle)
// PB3/RESET	not available, used for programming

__fuse_t __fuse __attribute__((section (".fuse"))) = {0xE2u, 0xDFu, 0xFFu};

const unsigned int PortADuetInputBit = 0;
const unsigned int AdcPhototransistorChan = 1;
#if DUAL_NOZZLE
const unsigned int AdcThermistor2Chan = 2;
const unsigned int PortASeriesResistorSenseBit = 3;
const unsigned int AdcThermistor1Chan = 4;
#else
const unsigned int PortADuet12KOutputBit = 2;
const unsigned int AdcThermistor1Chan = 3;
const unsigned int PortASeriesResistorSenseBit = 4;
#endif
const unsigned int PortAFanControlBit = 5;
const unsigned int PortANearLedBit = 6;
#if DUAL_NOZZLE
const unsigned int PortADuet12KOutputBit = 7;
#else
const unsigned int PortADuet10KOutputBit = 7;
#endif

const uint8_t PortAUnusedBitMask = 0;

const uint8_t PortBFarLedMask = BITVAL(0) | BITVAL(1);
#if DUAL_NOZZLE
const unsigned int PortBDuet10KOutputBit = 2;
const uint8_t PortBUnusedBitMask = 0;
#elif ISR_DEBUG
const unsigned int PortBDebugPin = 2;
const uint8_t PortBUnusedBitMask = 0;
#else
const uint8_t PortBUnusedBitMask = BITVAL(2);
#endif

// Approximate MPU frequency (8MHz internal oscillator)
const uint32_t F_CPU = 8000000uL;

// IR parameters. These also allow us to receive a signal through the command input.
const uint16_t interruptFreq = 8000;						// interrupt frequency. We run the IR sensor at one quarter of this, i.e. 2kHz
															// highest usable value is about 9.25kHz because the ADC needs 13.5 clock cycles per conversion.
const uint16_t divisorIR = (uint16_t)(F_CPU/interruptFreq);
const uint16_t baseTopIR = divisorIR - 1;
const uint16_t cyclesAveragedIR = 8;						// must be a power of 2, max 32 (unless we make onSumIR and offSumIR uint32_t)

const uint16_t farThreshold = 10 * cyclesAveragedIR;		// minimum far reading for us to think the sensor is working properly
const uint16_t simpleNearThreshold = 30 * cyclesAveragedIR;	// minimum reading to set output high in simple mode
const uint16_t saturatedThreshold = 870 * cyclesAveragedIR;	// minimum reading for which we consider the sensor saturated

// IR variables
typedef uint8_t invariant(value < cyclesAveragedIR) irIndex_t;

struct IrData
{
	uint16_t readings[cyclesAveragedIR];
	volatile uint16_t sum;
	irIndex_t index;

	void addReading(uint16_t arg)
	writes(*this; volatile)
	pre(invar())
	pre(arg <= 1023)
	post(invar())
	{
		sum = sum - readings[index] + arg;
		readings[index] = arg;
		index = static_cast<irIndex_t>((index + 1) % cyclesAveragedIR);
	}
	
	void init()
	writes(*this; volatile)
	post(invar());

	ghost(
		bool invar() const
			returns((forall r in readings :- r <= 1023) && sum == + over readings);
	)
	
#ifdef __ECV__
	// Dummy constructor to keep eCv happy
	IrData() : index(0) {}
#endif
};

IrData nearData, farData, offData;
	
// Fan parameters
const uint16_t thermistorSampleFreq = 16;
const uint16_t thermistorSampleIntervalTicks = interruptFreq/thermistorSampleFreq;

#if DUAL_NOZZLE
const uint16_t thermistorSamplesAveraged = 8;			// reduced from 16 because it looks like we ran out of memory in the dual nozzle case
#else
const uint16_t thermistorSamplesAveraged = 16;
#endif

// Fan thresholds

// Using a 1K series resistor, we use the ADC in differential mode with a gain of 1 and full scale resolution of 512, but we reverse the inputs so we effectively get 2x extra gain.
const uint16_t thermistorConnectedThreshold1K = 30;		// we consider the hot end thermistor to be disconnected if we get this reading less than the reference, or a higher reading
const uint16_t thermistorOffThreshold1K = 340;			// we turn the fan off if we get this reading less than the reference (about 38C), or a higher reading
const uint16_t thermistorOnThreshold1K = 400;			// we turn the fan on if we get this reading less than the reference (about 42C), or lower reading

// Using a 4K7 series resistor, we use the ADC in single-ended mode with a gain of 1.
const uint16_t thermistorConnectedThreshold4K7 = 7;		// we consider the hot end thermistor to be disconnected if we get this reading less than the reference, or a higher reading
const uint16_t thermistorOffThreshold4K7 = 78;			// we turn the fan off if we get this reading less than the reference (about 38C), or a higher reading
const uint16_t thermistorOnThreshold4K7 = 92;			// we turn the fan on if we get this reading less than the reference (about 42C), or lower reading

const uint16_t fanOnSeconds = 2;						// once the fan is on, we keep it on for at least this time

// Thermistor and fan variables
typedef uint8_t invariant(value < thermistorSamplesAveraged) thermistorIndex_t;

struct ThermistorData
{	
	uint16_t readings[thermistorSamplesAveraged], offsets[thermistorSamplesAveraged];
	volatile uint16_t readingSum, offsetSum;
	thermistorIndex_t index;

	void init(uint16_t readingInit, uint16_t offsetInit)
	writes(*this; volatile)
	pre(readingInit <= 1023; offsetInit <= 1023)
	post(this->invar());

	ghost(
		bool invar() const
		returns(   (forall r in readings :- r <= 1023)
				&& (forall r in offsets :- r <= 1023)
				&& readingSum == + over readings
				&& offsetSum == + over offsets
			   );
	)

#ifdef __ECV__
	// Dummy constructor to keep eCv happy
	IrData() : index(0) {}
#endif
};

ThermistorData thermistor1Data;
#if DUAL_NOZZLE
ThermistorData thermistor2Data;
#endif

uint16_t thermistorConnectedThreshold, thermistorOnThreshold, thermistorOffThreshold;
bool thermistor1Kmode;
uint16_t lastFanSampleTicks;
uint8_t fanChangeCount;

// General variables
volatile uint16_t tickCounter;						// counts system ticks, lower 2 bits also used for ADC/LED state
bool running;

/* ISR for the timer 0 compare match A interrupt
This works on a cycle of 16 readings as follows:

State	Just did	Doing now	New LED state	New ADC state
0		Dummy off	Far			Off				(Phototransistor)
1		Far			Off			Near			(Phototransistor)
2		Off			Near		Off				(Phototransistor)
3		Near		Dummy off	Far				(Phototransistor)
4		Dummy off	Far			Off				(Phototransistor)
5		Far			Off			Near			(Phototransistor)
6		Off			Near		Off				(Phototransistor)
7		Near		Dummy off	Far				(Phototransistor)
8		Dummy off	Far			Off				(Phototransistor)
9		Far			Off			Near			(Phototransistor)
10		Off			Near		Off				Thermistor
11		Near		Dummy fan	(Off)			(Thermistor)
12		Dummy fan	Dummy fan	(Off)			(Thermistor)
13		Dummy fan	Dummy fan	(Off)			(Thermistor)
14		Dummy fan	Fan			(Off)			Phototransistor
15		Fan			Dummy off	Far				(Phototransistor)

This pattern takes account of the following:
1. When we switch the ADC into differential mode to get reliable readings with a 1K series resistor, the ADC subsystem needs extra time to settle down.
2. We want to measure the readings with near and far LEDs illuminated from the off-state in both cases, so that the slow phototransistor response affects
   both readings equally.
*/

ISR(TIM1_COMPB_vect)
writes(nearData; farData; offData)
writes(thermistor1Data)
#if DUAL_NOZZLE
writes(thermistor2Data)
#endif
writes(volatile)
pre(nearData.invar(); farData.invar(); offData.invar())
pre(thermistor1Data.invar())
#if DUAL_NOZZLE
pre(thermistor2Data.invar())
#endif
post(nearData.invar(); farData.invar(); offData.invar())
post(thermistor1Data.invar())
#if DUAL_NOZZLE
post(thermistor2Data.invar())
#endif
{
#if ISR_DEBUG
	PORTB |= BITVAL(PortBDebugPin);					// set debug pin high
#endif

	uint16_t adcVal = ADC & 1023u;					// get the ADC reading from the previous conversion
	uint8_t locTickCounter = (uint8_t)tickCounter;
	while (TCNT1 < 3 * 64) {}						// delay a little until the ADC s/h has taken effect. 3 ADC clocks should be enough, and 1 ADC clock is 64 of our clocks.
	switch(locTickCounter & 0x0fu)
	{
		case 0:
		case 4:
		case 8:
			// Far LED is on, we just did a dummy off reading, we are doing a far reading now and an off reading next
			PORTB &= ~PortBFarLedMask;				// turn far LED off
			break;

		case 1:
		case 5:
		case 9:
			// LEDs are off, we just did a far reading, we are doing an off reading now and a near reading next			
			if (running)
			{
				farData.addReading(adcVal);
			}
			PORTA |= BITVAL(PortANearLedBit);		// turn near LED on
			break;

		case 2:
		case 6:
			// Near LED is on, we just did a, off reading, we are doing a near reading now and a dummy off reading next
			if (running)
			{
				offData.addReading(adcVal);
			}
			PORTA &= ~BITVAL(PortANearLedBit);		// turn near LED off
			break;

		case 3:
		case 7:
			// LEDs are off, we just did a near reading, we are doing a dummy off reading now and a far reading next
			if (running)
			{
				nearData.addReading(adcVal);
			}
			PORTB |= PortBFarLedMask;				// turn far LED on
			break;
			
		case 10:
			// Near LED is on, we just did an off reading, we are doing a near reading now and a fan reading next
			if (running)
			{
				offData.addReading(adcVal);
			}
			PORTA &= ~BITVAL(PortANearLedBit);		// turn near LED off

#if DUAL_NOZZLE
			if ((locTickCounter & 0x20u) == 0)
			{
				// Select thermistor 1
				if (thermistor1Kmode)
				{
					ADMUX = ((locTickCounter & 0x10u) != 0)
						? 0b00110011u				// +ve input = ADC4, -ve input = ADC3, gain x20
						: 0b00010011u;				// +ve input = ADC3, -ve input = ADC4, gain x20
				}
				else
				{
					ADMUX = (uint8_t)AdcThermistor1Chan;	// select thermistor 1 (ADC4) as a single-ended input
				}
			}
			else
			{
				// Select thermistor 2
				if (thermistor1Kmode)
				{
					ADMUX = ((locTickCounter & 0x10u) != 0)
						? 0b00010001u				// +ve input = ADC2, -ve input = ADC3, gain x20
						: 0b00110001u;				// +ve input = ADC3, -ve input = ADC2, gain x20
				}
				else
				{
					ADMUX = (uint8_t)AdcThermistor2Chan;	// select thermistor 2 (ADC2) as a single-ended input
				}
			}
#else
			if (thermistor1Kmode)
			{
				ADMUX = ((locTickCounter & 0x10u) != 0)
						? 0b00010011u				// +ve input = ADC3, -ve input = ADC4, gain x20
						: 0b00110011u;				// +ve input = ADC4, -ve input = ADC3, gain x20
			}
			else
			{
				ADMUX = (uint8_t)AdcThermistor1Chan;	// select thermistor 1 (ADC3) as a single-ended input
			}
#endif			
			break;
		
		case 11:
			// LEDs are off, we just did a near reading, we are doing a fan reading which we will discard, we will do another fan reading next
			if (running)
			{
				nearData.addReading(adcVal);
			}
			break;
			
		case 12:
		case 13:
			// LEDs are off and we are doing dummy fan readings
			break;

		case 14:
			// LEDs are off, we just did a dummy fan reading, we are doing another fan reading now and a dummy off reading next
			ADMUX = (uint8_t)AdcPhototransistorChan;	// select input 1 = phototransistor
			break;

		case 15:
			// LEDs are off, we just did a fan reading, we are doing an off reading now and a far reading next
			if (running)
			{
				ThermistorData* currentThermistor =
#if DUAL_NOZZLE
					((locTickCounter & 0x20u) == 0) ? &thermistor1Data : &thermistor2Data;
#else
					&thermistor1Data;
#endif
				if (thermistor1Kmode)
				{
					adcVal ^= 0x0200u;				// convert signed reading to unsigned biased by 512
					if ((locTickCounter & 0x10u) != 0)
					{
						currentThermistor->readingSum = currentThermistor->readingSum - currentThermistor->readings[currentThermistor->index] + adcVal;
						currentThermistor->readings[currentThermistor->index] = adcVal;
						currentThermistor->index = (currentThermistor->index + 1) & (thermistorSamplesAveraged - 1);
					}
					else
					{
						currentThermistor->offsetSum = currentThermistor->offsetSum - currentThermistor->offsets[currentThermistor->index] + adcVal;
						currentThermistor->offsets[currentThermistor->index] = adcVal;
					}
				}
				else
				{
					currentThermistor->readingSum = currentThermistor->readingSum - currentThermistor->readings[currentThermistor->index] + adcVal;
					currentThermistor->readings[currentThermistor->index] = adcVal;
					currentThermistor->index = (currentThermistor->index + 1) & (thermistorSamplesAveraged - 1);
				}
			}
			PORTB |= PortBFarLedMask;				// turn far LED on
			break;
	}
	
	++tickCounter;

#if ISR_DEBUG
	PORTB &= (uint8_t)(~BITVAL(PortBDebugPin) & 0xFFu);	// set debug pin high
#endif
}

// Delay for a little while
// Each iteration of the loop takes 4 clocks plus one clock per NOP instruction in the body.
// The additional overhead for the function, including calling it, is 12 clocks.
// Therefore, with F_CPU = 8MHz and using 4 NOP instructions, it delays n + 1.5 microseconds.
void shortDelay(uint8_t n)
{
	for (uint8_t i = 0; i < n; ++i)
	keep(i <= n)
	decrease(n - i)
	{
#ifndef __ECV__			// eCv doesn't understand asm
		asm volatile ("nop");
		asm volatile ("nop");
		asm volatile ("nop");
		asm volatile ("nop");
#endif
	}
}

// Check the fan
void checkFan()	
writes(fanChangeCount; volatile)
{
	if ((PORTA & BITVAL(PortAFanControlBit)) != 0)
	{
		// Fan is on. Turn it off if thermistor is connected and temp <= off-threshold
		if (   (thermistor1Data.readingSum < thermistor1Data.offsetSum)
#if DUAL_NOZZLE
			&& (thermistor2Data.readingSum < thermistor2Data.offsetSum)
#endif
		   )
		{
			uint16_t fanDiff1 = thermistor1Data.offsetSum - thermistor1Data.readingSum;
#if DUAL_NOZZLE
			uint16_t fanDiff2 = thermistor2Data.offsetSum - thermistor2Data.readingSum;
#endif
			if (   (fanDiff1 >= thermistorConnectedThreshold) && (fanDiff1 <= thermistorOffThreshold)
#if DUAL_NOZZLE
				&& (fanDiff2 >= thermistorConnectedThreshold) && (fanDiff2 <= thermistorOffThreshold)
#endif
			   )
			{
				if (fanChangeCount == 0)
				{
					PORTA &= (uint8_t)~BITVAL(PortAFanControlBit);	// turn fan off						
				}
				else
				{
					--fanChangeCount;
				}
			}
		}			
	}
	else
	{
		uint16_t fanDiff1;
#if DUAL_NOZZLE
		uint16_t fanDiff2;
#endif
		// Fan is off. Turn it on if thermistor is disconnected or temp >= on-threshold
		if (   (thermistor1Data.readingSum >= thermistor1Data.offsetSum)
			|| ((fanDiff1 = thermistor1Data.offsetSum - thermistor1Data.readingSum) < thermistorConnectedThreshold)
			|| (fanDiff1 >= thermistorOnThreshold)
#if DUAL_NOZZLE
			|| (thermistor2Data.readingSum >= thermistor2Data.offsetSum)
			|| ((fanDiff2 = thermistor2Data.offsetSum - thermistor2Data.readingSum) < thermistorConnectedThreshold)
			|| (fanDiff2 >= thermistorOnThreshold)
#endif
		   )
		{
			// We used to turn the fan on immediately, but now we delay it a little to try to improve noise immunity
			if (fanChangeCount >= fanOnSeconds * thermistorSampleFreq)
			{
				PORTA |= BITVAL(PortAFanControlBit);		// turn fan on			
			}
			else
			{
				fanChangeCount += 4;						// the time we wait before turning the fan on is 1/4 of the time we wait before turning it off
			}
		}		
	}
	
#ifndef __ECV__
	wdt_reset();											// kick the watchdog
#endif
}

// Give a G31 reading of about 0
inline void SetOutputOff()
writes(volatile)
{
	// We do this in 2 operations, each of which is atomic, so that we don't mess up what the ISR is doing with the LEDs.
#if DUAL_NOZZLE
	PORTB &= ~BITVAL(PortBDuet10KOutputBit);
	PORTA &= ~BITVAL(PortADuet12KOutputBit);
#else
	PORTA &= ~BITVAL(PortADuet10KOutputBit);
	PORTA &= ~BITVAL(PortADuet12KOutputBit);
#endif
}

// Give a G31 reading of about 465 indicating we are approaching the trigger point
inline void SetOutputApproaching()
writes(volatile)
{
	// We do this in 2 operations, each of which is atomic, so that we don't mess up what the ISR is doing with the LEDs.
#if DUAL_NOZZLE
	PORTB &= ~BITVAL(PortBDuet10KOutputBit);
	PORTA |= BITVAL(PortADuet12KOutputBit);
#else
	PORTA &= ~BITVAL(PortADuet10KOutputBit);
	PORTA |= BITVAL(PortADuet12KOutputBit);
#endif
}	

// Give a G31 reading of about 535 indicating we are at/past the trigger point
inline void SetOutputOn()
writes(volatile)
{
	// We do this in 2 operations, each of which is atomic, so that we don't mess up what the ISR is doing with the LEDs.
#if DUAL_NOZZLE
	PORTB |= BITVAL(PortBDuet10KOutputBit);
	PORTA &= ~BITVAL(PortADuet12KOutputBit);
#else
	PORTA |= BITVAL(PortADuet10KOutputBit);
	PORTA &= ~BITVAL(PortADuet12KOutputBit);
#endif
}
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
int main(void)
writes(volatile)
writes(running)
writes(nearData; farData; offData)	// IR variables
writes(thermistor1Data)
#if DUAL_NOZZLE
writes(thermistor2Data)
#endif
writes(fanChangeCount; lastFanSampleTicks)				// fan variables
writes(thermistor1Kmode; thermistorConnectedThreshold; thermistorOffThreshold; thermistorOnThreshold)
{
	cli();
#if DUAL_NOZZLE
	DIDR0 = BITVAL(AdcPhototransistorChan) | BITVAL(AdcThermistor1Chan) | BITVAL(AdcThermistor2Chan);
	// disable digital input buffers on ADC pins
#else
	DIDR0 = BITVAL(AdcPhototransistorChan) | BITVAL(AdcThermistor1Chan);
															// disable digital input buffers on ADC pins
#endif
	// Set ports and pullup resistors
	PORTA = BITVAL(PortADuetInputBit) | BITVAL(PortASeriesResistorSenseBit) | PortAUnusedBitMask;
															// enable pullup on Duet input, series resistor sense input, and unused I/O pins
	PORTB = PortBUnusedBitMask;								// enable pullup on unused I/O pins
	
	// Enable outputs
#if DUAL_NOZZLE
	DDRA = BITVAL(PortAFanControlBit) | BITVAL(PortANearLedBit) | BITVAL(PortADuet12KOutputBit);
#else
	DDRA = BITVAL(PortAFanControlBit) | BITVAL(PortANearLedBit) | BITVAL(PortADuet10KOutputBit) | BITVAL(PortADuet12KOutputBit);
#endif

#if DUAL_NOZZLE
	DDRB = PortBFarLedMask | BITVAL(PortBDuet10KOutputBit);	// enable LED and 12K outputs on port B
#elif ISR_DEBUG
	DDRB = PortBFarLedMask | BITVAL(PortBDebugPin);			// enable LED and debug outputs on port B
#else
	DDRB = PortBFarLedMask;									// enable LED outputs on port B
#endif
	
	// Wait 10ms to ensure that the power has stabilized before we read the series resistor sense pin
	for (uint8_t i = 0; i < 40; ++i)
	{
		shortDelay(255u);
	}
	thermistor1Kmode = ((PINA & BITVAL(PortASeriesResistorSenseBit)) != 0);
	
	// Initialize the fan so that it won't come on at power up
	uint16_t readingInit, offsetInit;
	if (thermistor1Kmode)
	{
		// When reading the thermistor in 1K series resistor mode, we run ADC in differential bipolar mode, gain = 20 (effective gain is 10 because full-scale is 512 not 1024)
		// We use the 1K mode sense pin as a +3.3V reference. Set it HIGH to reduce noise on it. We have already set the bit in the output register.
		DDRA |= BITVAL(PortASeriesResistorSenseBit);
		
		thermistorConnectedThreshold = thermistorConnectedThreshold1K * thermistorSamplesAveraged;
		thermistorOffThreshold = thermistorOffThreshold1K * thermistorSamplesAveraged;
		thermistorOnThreshold = thermistorOnThreshold1K * thermistorSamplesAveraged;
		offsetInit = 512;
		readingInit = offsetInit - thermistorConnectedThreshold1K;
	}
	else
	{
		// When reading the thermistor in 4.7K series resistor mode, we run ADC in single-ended mode, gain = 1
		thermistorConnectedThreshold = thermistorConnectedThreshold4K7 * thermistorSamplesAveraged;
		thermistorOffThreshold = thermistorOffThreshold4K7 * thermistorSamplesAveraged;
		thermistorOnThreshold = thermistorOnThreshold4K7 * thermistorSamplesAveraged;
		offsetInit = 1023;
		readingInit = offsetInit - thermistorConnectedThreshold4K7;
	}

	thermistor1Data.init(readingInit, offsetInit);
#if DUAL_NOZZLE
	thermistor2Data.init(readingInit, offsetInit);
#endif

	sei();

#ifndef __ECV__												// eCv++ doesn't understand gcc assembler syntax
	wdt_enable(WDTO_500MS);									// enable the watchdog (we kick it when checking the fan)	
#endif
		
	runIRsensorAndFan();									// doesn't return
	return 0;												// to keep gcc happy
}

// Initialize the IR data structure
void IrData::init()
{
	for (uint8_t i = 0; i < cyclesAveragedIR; ++i)
	writes(i; *this; volatile)
	keep(i <= cyclesAveragedIR)
	keep(forall j in 0..(i-1) :- readings[j] == 0)
	decrease(cyclesAveragedIR - i)
	{
		readings[i] = 0;
	}
	index = 0;
	sum = 0;
}

// Initialize the thermistor data structure
void ThermistorData::init(uint16_t readingInit, uint16_t offsetInit)
{
	readingSum = 0;
	offsetSum = 0;

	for (uint8_t i = 0; i < thermistorSamplesAveraged; ++i)
	writes(i; *this; volatile)
	keep(i <= thermistorSamplesAveraged)
	keep(forall j in 0..(i - 1) :- readings[j] == readingInit)
	keep(forall j in 0..(i - 1) :- offsets[j] == offsetInit)
	keep(readingSum == + over readings.take(i))
	keep(offsetSum == + over offsets.take(i))
	decrease(thermistorSamplesAveraged - i)
	{
		readings[i] = readingInit;
		readingSum += readingInit;
		offsets[i] = offsetInit;
		offsetSum += offsetInit;
	}
	index = 0;
}

// End

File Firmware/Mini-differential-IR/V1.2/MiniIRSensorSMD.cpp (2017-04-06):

/*
 * MiniIRSensorSmd.cpp
 *
 * Created: 29/07/2016 18:02:05
 * Author : David
 */ 

#include "ecv.h"

#ifdef __ECV__
#define __attribute__(_x)
#define __volatile__
#endif

#ifdef __ECV__
#pragma ECV noverifyincludefiles
#endif

#include <avr/io.h>
#include <avr/interrupt.h>
#include <avr/eeprom.h>
#include <avr/wdt.h>

#ifdef __ECV__
#pragma ECV verifyincludefiles
#undef cli
#undef sei
extern void cli();
extern void sei();
#endif

#define SUPPORT_CALIBRATION	(0)
#define RANGE_DEBUG			(0)		// set nonzero to flash LED when it changes range

#define BITVAL(_x) static_cast<uint8_t>(1u << (_x))

// Pin assignments:
// PB0/MOSI			far LED drive, active high
// PB1/MISO			near LED drive, active high
// PB2/ADC1/SCK		output to Duet via 12K resistor
// PB3/ADC3			output to Duet via 10K resistor
// PB4/ADC2			input from phototransistor
// PB5/ADC0/RESET	not available, used for programming

#ifndef __ECV__
__fuse_t __fuse __attribute__((section (".fuse"))) = {0xE2u, 0xDFu, 0xFFu};
#endif

const unsigned int AdcPhototransistorChan = 2;				// ADC channel for the phototransistor
const unsigned int AdcPortBDuet3K0OutputChan = 3;			// ADC channel for the 3K0 and LED output bit, when we use it as an input
const unsigned int AdcPortBDuet3K6OutputChan = 1;			// ADC channel for the 3K6 output bit, when we use it as an input
const unsigned int PortBNearLedBit = 1;
const unsigned int PortBFarLedBit = 0;
const unsigned int PortBDuet3K0OutputBit = 3;
const unsigned int PortBDuet3K6OutputBit = 2;

const uint8_t PortBUnusedBitMask = 0;

// Approximate MPU frequency (8MHz internal oscillator)
const uint32_t F_CPU = 8000000uL;

// IR parameters. These also allow us to receive a signal through the command input.
const uint16_t interruptFreq = 8000;						// interrupt frequency. We run the IR sensor at one quarter of this, i.e. 2kHz
															// highest usable value is about 9.25kHz because the ADC needs 13.5 clock cycles per conversion.
const uint16_t divisorIR = (uint16_t)(F_CPU/interruptFreq);
const uint16_t prescalerIR = 8;								// needs to be high enough to get baseTopIR below 256
const uint16_t baseTopIR = (divisorIR/prescalerIR) - 1u;
const uint16_t cyclesAveragedIR = 8;						// must be a power of 2, max 64 (unless we make onSumIR and offSumIR uint32_t)
															// *** max is now 16 because we add the 3 sums when we sense the pullup resistor ***

const uint16_t farThreshold = 10u * cyclesAveragedIR;		// minimum far reading for us to think the sensor is working properly
const uint16_t saturatedThreshold = 870u * cyclesAveragedIR; // minimum reading for which we consider the sensor saturated
const uint16_t rangeUpThreshold = 700u;						// must be less than saturatedThreshold
const uint16_t rangeDownThreshold = 120u;					// must be less than about 1/5 rangeUpThreshold

const uint16_t ledFlashTime = interruptFreq/6u;				// how long the LED is on or off for when we are flashing it

// IR variables
typedef uint8_t invariant(value < cyclesAveragedIR) irIndex_t;

struct IrData
{
	uint16_t readings[cyclesAveragedIR];
	volatile uint16_t sum;
	irIndex_t index;

	void addReading(uint16_t arg)
	writes(*this; volatile)
	pre(invar())
	pre(arg <= 1023)
	post(invar())
	{
		sum = sum - readings[index] + arg;
		readings[index] = arg;
		index = static_cast<irIndex_t>((index + 1u) % cyclesAveragedIR);
	}
	
	void init()
	writes(*this; volatile)
	post(invar());

	ghost(
		bool invar() const
			returns((forall r in readings :- r <= 1023) && sum == + over readings);
	)
	
#ifdef __ECV__
	// Dummy constructor to keep eCv happy
	IrData() : index(0) {}
#endif
};

IrData nearData, farData, offData;
	
// General variables
volatile uint16_t tickCounter = 0;					// counts system ticks, lower 2 bits also used for ADC/LED state

#if SUPPORT_CALIBRATION

const uint16_t eepromMagic = 0x52A6;

struct NvData
{
	uint16_t nearMultiplier;
	uint16_t farMultiplier;
	uint16_t checksum;
} nvData;

#endif

bool digitalOutput = false;
volatile bool running = false;						// volatile because we care about when it is written

#if SUPPORT_CALIBRATION

// EEPROM access functions
void readEEPROM(uint8_t ucAddress, uint8_t *p, uint8_t len)
pre(len != 0)
{
	do
	{
		/* Wait for completion of previous write */
		while(EECR & (1<<EEPE))
		;
		/* Set up address register */
		EEAR = ucAddress++;
		/* Start eeprom read by writing EERE */
		EECR |= (1<<EERE);
		/* Return data from data register */
		*p++ = EEDR;
	} while (--len != 0);
}

void writeEEPROM(uint8_t ucAddress, const uint8_t *p, uint8_t len)
pre(len != 0)
{
	do
	{
		/* Wait for completion of previous write */
		while(EECR & (1<<EEPE))
		;
		/* Set Programming mode */
		EECR = (0<<EEPM1)|(0<<EEPM0);
		/* Set up address and data registers */
		EEAR = ucAddress++;
		EEDR = *p++;
		/* Write logical one to EEMPE */
		EECR |= (1<<EEMPE);
		/* Start eeprom write by setting EEPE */
		EECR |= (1<<EEPE);
	} while (--len != 0);
}

#endif

// ISR for the timer 0 compare match interrupt
// This uses 19 bytes of stack (from assembly listing, 2016-07-30)
#ifdef __ECV__
void TIM0_COMPB_vect()
#else
ISR(TIM0_COMPB_vect)
#endif
writes(nearData; farData; offData)
writes(volatile)
pre(nearData.invar(); farData.invar(); offData.invar())
post(nearData.invar(); farData.invar(); offData.invar())
{
	const uint16_t adcVal = ADC & 1023u;			// get the ADC reading from the previous conversion
	const uint8_t locTickCounter = (uint8_t)tickCounter;
	while (TCNT0 < 3u * 8u) {}						// delay a little until the ADC s/h has taken effect. 3 ADC clocks should be enough, and 1 ADC clock is 8 timer 0 clocks.
	switch(locTickCounter & 0x03u)
	{
		case 0:
			// Far LED is on, we just did no reading, we are doing a far reading now and an off reading next
			PORTB &= ~BITVAL(PortBFarLedBit);		// turn far LED off
			break;
		
		case 1:
			// LEDs are off, we just did a far reading, we are doing a off reading now and a near reading next			
			if (running)
			{
				farData.addReading(adcVal);
			}
			PORTB |= BITVAL(PortBNearLedBit);		// turn near LED on
			break;
					
		case 2:
			// Near LED is on, we just did an off reading, we are doing a near reading now and a dummy off reading next
			if (running)
			{
				offData.addReading(adcVal);
			}
			PORTB &= ~BITVAL(PortBNearLedBit);		// turn near LED off
			break;

		case 3:
			// Far LED is on, we just did an off reading, we are doing another off reading now which will be discarded
			if (running)
			{
				nearData.addReading(adcVal);
			}
			PORTB |= BITVAL(PortBFarLedBit);		// turn far LED on
			break;
	}
	++tickCounter;
}

// Give a G31 reading of about 0
inline void SetOutputOff()
writes(volatile)
{
	// We do this in 2 operations, each of which is atomic, so that we don't mess up what the ISR is doing with the LEDs.
	PORTB &= ~BITVAL(PortBDuet3K0OutputBit);
	PORTB &= ~BITVAL(PortBDuet3K6OutputBit);
}
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

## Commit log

2014-03-16 Added STL files
    Added STL files for the printed parts needed to use the new sensor
    board, along with some other printed parts for the Ormerod
    [BoardHolder.scad, BoardHolder.stl, FanDeflector.scad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]
2014-03-16 Added schematic, board layout and circuit notes
    [ModulatedIRSensor.brd, ModulatedIRSensor.sch, Ormerod sensor board all kits BOM.ods]
2014-03-20 Added fan deflector aerofoil
    [fan_deflector_v4_aerofoil.scad]
2014-03-24 Added new parts
    [Insulator-thick.scad, Insulator-thick.stl, one-piece-hotend-airduct-with-new-irsensor-2.scad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]
2014-03-26 Updated BOM
    [Ormerod sensor board all kits BOM.ods]
2014-03-27 Added insulator that holds ultrasonic transducer
    [Insulator-for-ultrasonic-2.scad, Insulator-for-ultrasonic-2.stl]
2014-03-27 Update readme.md
    Added description of insulator with holder for the ultrasonic transducer
2014-03-28 Changed insulator for ultrasonic transducer
    Modified the design of the insulator with a holder for the ultrasonic
    transducer to reduce the depth of the countersink, so that the screws
    only protrude 3mm beyond the back of the PCB. Added a cutout to allow
    in-situ programming.
    [Insulator-for-ultrasonic.scad, Insulator-for-ultrasonic.stl]
2014-04-04 Added sensorpad.scad and .stl
    [sensorpad.scad, sensorpad.stl]
2014-04-04 Added description of sensorpad.stl to readme file
2014-05-04 Added modified sensor pad and button push
    Added a modified version of the add-on sensor pad that places the homing
    tab nearer the z-screw and avoids fouling the z stepper motor shaft
    [OrmerodButtonPush.scad, OrmerodButtonPush.stl, sensorpad-modified.scad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]
2014-05-29 Added cutout to access ICSP contacts
    Added a cutout to the insulator so that the ICSP contacts for
    reprogramming the mcu can be accessed in-situ.
    [Insulator.scad]
2014-05-29 Added capsense variant of the insulator
    Added a variant of the sensor board insulator to suit the prototype
    (hacked) capacitive height sensing board
    [Insulator-capsense.scad, Insulator-capsense.stl]
2014-05-29 Add X-carriage design
    Added .scad and .stl files for Ormerod X-carriage
    [Xcarriage.scad, Xcarriage.stl]
2014-06-19 Added sensor pad for diff IR sensor
    Also deleted some obsolete files
    [BoardHolder-diff-led.scad, BoardHolder-diff-led.stl, Insulator-diff-led.scad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]
2014-06-20 Various parts updated
    Reduced tab width for differential IR sensor pad
    Adjusted spacing for differential IR sensor board holder
    Tidied up fan inlet duct and made some dimensions configurable
    [BoardHolder-diff-led.scad, BoardHolder-diff-led.stl, FanDeflector.scad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]
2014-06-23 Added nozzle mount
    [NozzleMount.scad, NozzleMount.stl]
2014-06-24 Added differential LED board schematic
2014-06-24 Nozzle mount now configured for 2 nozzles
    [NozzleMount.scad, NozzleMount.stl]
2014-06-26 Added revised modified heatsink duct
    Added new version of modified heatsink duct based on importing RRP's
    original one into OpenScad. Also made sensor pad 1mm wider.
    [Modified-heatsink-duct-old.stl, Modified-x-motor-bracket-old.stl, modified-heatsink-duct.scad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]
2014-07-04 Rearranged folders and added diff LED firmware
    [ModulatedIRSensor.brd, ModulatedIRSensor.sch, Ormerod sensor board all kits BOM.ods]
2014-07-04 Added differential LED sensor circuit notes
2014-07-10 Corrected nozzle mount and added fan duct
    Increased the size of the slots in the nozzle mount to clear the brass
    Bowden end
    Added modified-fan-duct, which is RRP's fan duct with the cable tie loop
    cut off (the cable tie loop gets in the way of my hot end board)
    [NozzleMount.scad, NozzleMount.stl, modified-fan-duct.scad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]
2014-07-10 Added first attempt at Duet+Duet4X enclosure
    [DuetEnc.scad]
2014-07-10 Corrections to Duet_X4 enclosure
    Moved X4 lower standoffs an extra 2mm apart to match X4 board
    Increased Duet standoff radius by 0.1mm because slic3r was generating 2
    circles to print it instead of 3
    Added extra 1mm clearance for ribbon cable at top of box when X4 option
    is enabled
    [DuetEnc.scad, DuetEnc.stl]
2014-07-11 Minor corrections to Duet+X4 enclosure
    [DuetEnc.scad, DuetEncX4.stl]
2014-07-11 Added options for dual nozzle conversion
    Added options to the modified heatsink duct and the insulator to suit
    the dual nozzle conversion. The standoffs on the heatsink duct for
    fitting the sensor board need to be deeper for the dual nozzle, to give
    adequate clearance between the sensor components and the nearer of the
    two heater blocks. The insulator pillars are made thinner to compensate
    in part.
    [Insulator-diff-led-dual-nozzle.stl, Insulator-diff-led.scad, modified-heatsink-duct-dual-nozzle.stl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]
2014-07-14 Corrected insulator countersinks with short pillars
    Corrected the differential LED sensor insulating plate so that when the
    pillars are very short (e.g. with the dual nozzle option selected), the
    countersinks for the mounting screws are in the right place
    [Insulator-diff-led-dual-nozzle.stl, Insulator-diff-led.scad]
2014-07-14 Corrections for X4 variant
    Increased board depth so that the lid should fit
    Adjusted positions of cutouts for Duet connectors and SD card
    [DuetEnc.scad, DuetEncX4.stl]
2014-07-18 Amended nozzle mount to support 3 cutouts
    The nozzle mount now supports 3 cutouts so that it can be used with
    single nozzle heads (with modified heatsink block) and dual nozzle
    heads. Also increased side of Bowden slots a little.
    [NozzleMount-1or3.stl, NozzleMount.scad]
2014-07-26 Added an angle to the nozzle mount
    Changed the nozzle mount design to allow it to be angled to correct for
    head sag
    [NozzleMount-1or3-3deg.stl, NozzleMount-1or3.stl, NozzleMount.scad]
2014-08-04 Improved enclosure design + long nozzle mount option
    Improved the Duet+X4 enclosure design by strengthening the mounting
    pillars and adding access holes for the X4 power terminal screws. Also
    added an option on the nozzle mount to make it long, to help get started
    with ABS printing.
    [DuetEnc.scad, DuetEncX4.stl, NozzleMount-1or2-2deg-long.stl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]
2014-08-06 Added 'long' option to go with long nozzle mount
    [sensorpad-diff-led.scad]
2014-08-14 Fan deflector now has 4 screw holes
    Added 2 more screw holes to the fan deflector. This allows 4 mounting
    screws to be used to hold the fan to the heatsink, to avoid distorting
    the fan, which can make it noisy.
    [FanDeflector.scad, FanDeflector.stl]
2014-08-14 Added modified version of iambury's extruder gears
    Added a version of iamburny's double helix extruder gears, modified to
    make the holes for the motor shaft and the hex bolt customisable. Before
    I did this and increased the sizes, I found they were too tight to fit
    on the motor and the bolt.
    [iamburnyExtruderGearsModified.scad]
2014-08-18 Updated button push
    Updated the button push model to make the lengths configurable.
    Increased the default length to work with the Duet+DueX4 enclosure.
    [OrmerodButtonPush.scad, OrmerodButtonPush.stl]
2014-09-03 Added standard nozzle mount
    [NozzleMountStandard-2deg.stl]
2014-10-15 Added heatsink duct with board lowered by another 0.5mm
    [BoardHolder-diff-led.scad, BoardHolder-diff-led.stl, NozzleMount.scad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]
2014-10-28 Updated schematic and firmware for 2 nozzle
    Added the schematic for the 2-nozzle board. Updated the firmware source
    code to support the 2-nozzle board.
2015-01-06 Improved some models
    Improved model of Duet enclosure for Mini Kossel, and checked in some
    changes to iamburny's extruder gears
    [DuetEnc-MiniKossel.scad, DuetEnc-MiniKossel.stl, iamburnyExtruderGearsModified.scad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]
2015-05-05 Updated firmware for dual board
    Updated the firmware for the dual nozzle board to use the same offset
    cancellation technique as the single nozzle board when reading the
    thermistors. Reduced the number of thermistor samples averaged for the
    dual board to avoid running out of RAM. Also added holders for dual
    nozzle and mini boards.
    [BoardHolder-diff-led-dual.scad, BoardHolder-diff-led-mini.scad]
2015-05-05 Added orthogonal calibration piece
    Added a configurable orthogonal calibration piece so that it can be made
    small enough to use on the Mini Kossel
    [DuetEncMeasure.scad, OrthogonalCalibrationPiece.scad]
2015-05-05 Added STL for the orthogonal calibration piece
    [OrthogonalCalibrationPiece.stl]
2015-05-06 Added mini differential IR schematic and firmware
2015-06-09 New modulation order
    Changed modulation order to avoid an additional false trigger height
    above white surfaces following increase in sensitivity to better work
    with BuildTak as a target
    [MiniLedSensor.cpp, OrmerodLedSensor.cpp]
2016-01-20 Updated firmware and schematic to version 1.1a
    Updated the firmware and schematic to correspond with version 1.1a
    production boards
2017-04-06 Update firmware and schematic tio versoin 1.2

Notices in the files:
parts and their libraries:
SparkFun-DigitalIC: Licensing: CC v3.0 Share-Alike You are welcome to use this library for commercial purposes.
